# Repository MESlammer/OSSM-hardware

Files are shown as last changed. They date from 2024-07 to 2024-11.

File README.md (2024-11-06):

# OSSM - Open Source Sex Machine



OSSM (pronounced like "Awesome") is a user friendly every day sex machine for the people.

This project aims to help people curious about sex machines explore their interest. A second objective is optionally
learning how mechanics, electronics, physics and computing are involved in your sexual pleasure.

Please note that this is a _work in progress_ and we have attempted to keep compatibility with the current BOM going
forward, but it's not guaranteed.

_Our Primary design goals_ are to make a machine that is compact, quiet, of moderate cost, 3D printable (no
cutting/machining required), flexible, highly performant, with easily sourced components, and doesn't look like a giant
machine.
<p align="center">

</p>

### Is it actually Open Source?

It is one of a kind Certified, Actual, Factual, Open Source

[](https://certification.oshwa.org/ca000057.html)

## Getting Started

### [Read the Frequently Asked Questions](FAQ.md)

There are a few hardware flavours to choose from, we've included community modified versions in case that fits your use
case better!

### [Build Instructions](Documentation/Assembly%20Instructions.pdf)

### [Build Videos]("https://youtube.com/playlist?list=PLzSK7OAu3KNQsFo6WJGT8P28lfkD3xpps")

[Join our Discord](https://discord.gg/MmpT9xE) to be part of the discussion and get help with your build. We have a huge community of
makers!

<p align="center">

</p>

### Software

The software is available in this github repository. It is written and compiled utilizing PlatformIO on Visual Studio
Code. [Reference for working with the code in PlatformIO here](OSSM PlatformIO Readme.md)

We recommend using
the [Research and Desire Reference Board](https://shop.researchanddesire.com/products/ossm-reference-board) as Do It
Yourself by someone without extensive electronics knowledge creates a lot of support overhead. This code is still
arduino IDE compatible but offers many times better performance. Web based control is projected to be available in Feb 2025.  
### Eagle PCB

Simple PCB to power an ESP32 (wifi enabled microcontroller) from 24V and breakout the pins for the OSSM control

### Mechanical design

The OSSM use a compact belt design with components that have become widely available due to 3D printing popularity.
It is driven by a Nema23 motor of **your** choosing, although we reccomend small integrated closed loop servos for their
silent operation and very high performance.
<p align="center">

</p>

### Mounting

We have a new stand design you can check out on onshape!
[OnShape link](https://cad.onshape.com/documents/d520ea9a8cadb4ae8681f59b/w/00b211a6fa3b76c59ef28f4e/e/5f2c80d9d9c2433a7be7f789)

OSSM on mounting solution

### Safety

The safety of the OSSM build is yet to be fully characterized as it is a work in progress. The OSSM is a framework for
building your own sex machine and as such your specific combination may have risks not inherent to other builds. These
risks may be undocumented or undiscovered. Please see the [Hazards](Documentation/Hazards.md) file for more
information.

While using the OSSM we can suggest the following hierarchy of safety, however it is up to you and your build to decide
what risks exist and how to mitigate them.

1. Have ability to move away
2. Have ability to remove the power
3. If you are in bondage, safety is responsibility of the Top

## Bill Of Materials

We are calling this the reference build, when deviating from it please check compatability with existing Bill Of
Materials (BOM)

1.  **[3D Printed Parts](Hardware/OSSM%20Printed%20Parts)**
    - This has recently had significant changes
    - [Make sure to choose one of the options for the toy adapters](Hardware/OSSM%20Printed%20Parts/end%20effector%20options)
    - There are several mounting options available, the most popular being  
      the [Ulanzi Ball head mount](Hardware/OSSM%20Mounting) or  
      the [Shicks mount](Hardware/OSSM%20Mounting/Shicks%204040%20mount)
    - Thank you @Elims for the [belt tensioner design]( https://github.com/theelims )

2.  **IHSV57 NEMA23 Servo with 8mm shaft** _or_ **57AIM30 (Gold Motor)**:
    - **Gold Motor**
      - New standard motor for OSSM, please see [Gold Motor Info](Documentation/Gold-Motor.md) while docs are being updated.
        This motor is cheaper, more compact and has improved features which are being implemented in OSSM firmware.
      - For the latest information about this change, join the KinkyMakers Discord.
    - **iHSV57 (Previous Standard Motor)**
      - _Avoid the StepperOnline version_
      - Make sure you get something with **8mm** shaft.
      - There are **3** sizes of this motor:  
          100W = [iHSV57-30-**10**](https://www.aliexpress.com/w/wholesale-iHSV57%2525252d30%2525252d10.html)

          140W = [iHSV57-30-**14**](https://www.aliexpress.com/w/wholesale-iHSV57%2525252d30%2525252d14.html)

          180W = [iHSV57-30-**18**](https://www.aliexpress.com/w/wholesale-iHSV57%2525252d30%2525252d18.html)

      - We recommend motors with firmware version 6 (shown as `V60x`). Pay attention to
        this, [the firmware version is printed on the label on the side.](https://user-images.githubusercontent.com/131713378/234460307-1c29c18b-3bb5-4ac9-b66f-0dea9df0acac.png)
        You cannot update the motor firmware. version 5 will work, but it is not as feature rich for potential new
        features.
      - Search around for the best deal for you - we reccommend searching "ihsv57" on Aliexpress.com and choosing the -10
        -14 or -18. Some example listings:

        [AliExpress - US](https://www.aliexpress.us/item/2251832528412325.html)

        [AliExpress - CA & AU](https://www.aliexpress.us/item/32714727077.html)

      - For details on picking the right motor for your use case - check
          this [FAQ](FAQ.md#q--what-strength-of--motor-do-i-need)
      - If you are using the 140W or 180W version it is recommended to use a 10mm wide belt and pulley (see the next two items)

3.  **GT2 Pulley 8mm Bore 20 Tooth, 10mm width** :

    [Amazon - CA](https://www.amazon.ca/Timing-Pulley-8mm-bore-10mm-belt-20-Tooth/dp/B09L7D7HHT)

    [Amazon - US](https://www.amazon.com/WINSINN-Aluminum-Synchronous-Timing-Printer/dp/B07BTDRW5Z)

    [Banggood - AU](https://au.banggood.com/5MM-or-6_35MM-or-8MM-Bore-20TeethGT2-Alumium-Timing-Pulley-For-Width-10mm-GT2-Belt-p-1106314.html)

4.  **GT2 Timing Belt - 10mm width** :

    [Amazon - CA](www.amazon.ca/Timing-Meters-Creality-Anycubic-Printer/dp/B097T4DFM6)

    [Amazon - US](https://www.amazon.com/Timing-Meters-Creality-Anycubic-Printer/dp/B097T4DFM6)

    [Amazon - AU]()

    - Your desired stroke length plus about 200mm should be your minimum order length

5.  **Bearings** MR115-2RS 5x11x4mm :
    [Amazon - CA](https://www.amazon.ca/gp/product/B07CVBW44R)

    [Amazon - US](https://www.amazon.com/Miniature-Bearings-MR115-2RS-Double-Shielded-5x11x4mm/dp/B08PFT72RQ)

    [Aliexpress - AU](https://www.aliexpress.us/item/2251832628223170.html)

6.  **MGN12H Rail and bearing** :

    [Amazon - CA](https://www.amazon.ca/MGN12H-Stainless-Carriage-Precision-Machine/dp/B09TWKWCZR)

    [Amazon - US](https://www.amazon.com/ReliaBot-Linear-Carriage-Printer-Machine/dp/B07B4DWWZC)

    [Aliexpress - AU](https://www.aliexpress.com/item/32840113910.html)

    - Minimum 250mm in length, suggested 350mm
    - Rail length = desired stroke + 180mm
    - Must be MGN**12H** rail - H is a longer car than C which gives greater stability. 12 indicates 12mm rail width.

7.  **Power Supply**: 24 volt 4-5 amp w/ 2.1mm barrel DC plug

    - Larger motors generally need more power!  
      180W -> 24V 5A suggested minimum  
      140W -> 24V 4A suggested minimum  
      100W -> 24V 4A suggested minimum

    - See the FAQ for more details about power supply sizing based on real world experience of OSSM users.
    - The OSSM will work with small power supplies, but will be limited on maximum force.
    - Ensure the power supply is fully enclosed and shielded to avoid cross talk from electromagnetic interference (like a laptop power supply).
    - Ensure the power supply has the correct approvals for your location - This really helps ensure performance as well! (UL, CE, etc.)
    - It is strongly recommended that you purchase a good quality PSU such as a Meanwell.

8.  **Metric Hex Cap Screws** :  
    [Amazon - CA & US](https://www.amazon.ca/Comdox-500pcs-Socket-Screws-Assortment/dp/B06XQLTLHP)

    [Amazon - AU](https://www.amazon.com.au/VIGRUE-Stainless-Hexagon-Washers-Assortment/dp/B08CK9Y971) (this is a little
    expensive, we are looking for a cheaper alternative)

    - A kit like the ones above will provide what's needed:
    - 4x m5x20
    - 1x m5x12 (can also use m5x20)
    - 10x m3x8
    - 2x m3x16
    - 8x m5 nuts
    - 8x m3 nuts

9.  **ESP32 Development Board**
    - [An official OSSM reference PCB](https://research-and-desire.myshopify.com/collections/all/products/ossm-reference-board)
    - We do not currently have a best suggestion if you are not using a reference board, most generic development boards are the same
    - We have found that the 3.3v boards may miss steps at high speed, so please use a level shifter as well.
    - To start working on the project, something like this [Adafruit board](https://www.adafruit.com/product/3405) is an excellent place to start.
    - Accessories required for prototyping
      include [Breadboard](https://www.amazon.ca/Breadboard-Solderless-Prototype-Distribution-Connecting/dp/B01EV6LJ7G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)
      and [Dupont Jumpers](https://www.amazon.ca/120pcs-Multicolored-Breadboard-Arduino-raspberry/dp/B01LZF1ZSZ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)

### Octopart Links for ease of ordering and tracking

A list of non-3d printed supplies in one place. Most of the parts aren't available through the preferred Octopart
vendors but it still makes for a convenient list.

[Octopart - Collected Bill of Materials for US Suppliers](https://octopart.com/bom-tool/nfUsbySS)

## Official OSSM Wiring

OSSM reference board front
The above image is of a version 1 reference board.

### OSSM PCB Connections

OSSM PCB connection diagram

### GPIO Layout

OSSM pinout diagram
JST Header location with pin labels

## Non-Official OSSM Wiring

This should be a good start for the wiring of your OSSM! However, depending on your hardware mix settings or wiring may
be different

### OSSM PCB w/ TB6600 Stepper Driver



### Servo Wiring

ServoWiring

### Stepper Wiring

wiring notes

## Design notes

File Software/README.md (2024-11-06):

# Software
This is the recommended software for use with OSSM designs

## Requirements:
- Arduino IDE or PlatformIO
- ESP32 microcontroller

To use with Arduino, simply open the .ino file in the src directory. You will also need to copy the folders in the lib directory to your arduino library folder on your PC.

Use the tutorial below to install the ESP32 board into your Arduino IDE so you're ready to program!

[Setting up ESP32 on Arduino IDE](https://randomnerdtutorials.com/installing-the-esp32-board-in-arduino-ide-windows-instructions/)

If you aren't sure what ESP board to select in Arduino IDE, choose "ESP32 Dev Module" - it works on all ESP32 I have tested so far.

ESP32 Architecture

## Logging

This project uses ESP32's [native logging library](https://docs.espressif.com/projects/esp-idf/en/stable/esp32/api-reference/system/log.html).

## Commands

**Upload and monitor**
```bash
pio run -t upload -t monitor
```

**Run Unit Test tests**
```bash
pio test -e test
```

## Other Documentation
- [Git Branching Strategy](docs/Git Branching Strategy)

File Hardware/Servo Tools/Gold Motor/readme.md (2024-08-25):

<h1> New Web Serial tool </h1>

in the "Javascript GMP" folder run the page in some browser that supports web serial and hopefully it'll just work. 



<h1> Old Python Script </h1>
This pyhton script will write the default changes to the gold motor and show all the current settings in mostly english



the settings we change by default are



Watch out, I got tired of using the tool provided by the vendor and this was done quickly one night with ChatGPT as my copilot...

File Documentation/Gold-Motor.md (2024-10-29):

# New Standard Servo Motor

## 57AIM30 - Gold Motor

We have been testing and have decided on a new motor as the build standard. It has the same mounting pattern and shaft diameter as the old motor (iHSV57-30-XX).
It is sold by Research and Desire as [Gold Motor](https://www.researchanddesire.com/products/ossm-motor-gold-motor) or available generically as 57AIM30

If you wish to order a 57AIM30, you should source a model that runs at 1500 RPM and has an RS485 interface (NOT the 3000 RPM or CANBUS versions)

Also note that if you source your motor from somewhere other than R&D, you will need to reprogram the stored settings with a USB to RS485 dongle using the scripts found [here](https://github.com/KinkyMakers/OSSM-hardware/tree/master/Hardware/Servo%20Tools/Gold%20Motor) before you can use it.

Advantages:

- Cheaper (20%) - dependant on availability and location.
- Smaller (40% length of 180W standard - i.e. 60% reduction!).
- Lighter (50% weight of 180W).
- Higher peak force (30% higher in real-world test).
- Better over-torque handling - can be configured to reduce torque output instead of disable like current 180w servo.
- Is drop-in replacement for iHSV57 series making BOM compatible.

Requirements:
- Requires V2.2 PCB or newer for  simple wiring with PH-4 cable
  - Older boards will need wires soldered to 10 pin header
  - Recommend adding 1500uF capacitor, min 50V to older boards <V2.3

Disanvantages:

- More efficient (this causes more regenerated power in some motion conditions which requires additional capacitance and handling on the PCB).
  - PCB v2.3 as currently sold by R&D or listed on this repo has added capacitor. If you are upgrading your motor, you should add the capacitor as shown below.
- Digital comms over RS485 (Not worse than current RS232, just current boards don't have the needed adapter).
- Requires software setup to see full benefits (default FW settings disable motor in over-torque condition).
- If modding your software, technically lower top speed than HSV. (Standard code speed limit is lower than gold motor limit, so not a disadvantage for regular user).

## 42AIM30 - Gold Motor 42 (variant)

In addition to 57AIM30 (Gold Motor), which fits exactly to the previous designs and specs with no extra work, there is a varient motor which has exactly same internals and specs.
The 42AIM30 (see notes above for ordering the correct model) does away with the heatsink housing and is purely the cylindrical motor with connectors at the base.

Advantages (compared to 57AIM30):

- Smaller diameter (26%) - plus cylinder vs square.
- Lighter (unknown - ~25%?) - please submit mass if you have one.

Disadvantages (compared to 57AIM30):

- Much harder to mount.
  - No _mounting ears_ to bolt through, must put exact length machine screws into face of motor.
  - Current standard housings are not compatible with 42AIM30, though there are some options available via discord.
- Suspected heat issues caused by lack of heat sink and enclosure in printed housing - more data needed.
- Lack of clear advantages over Gold Motor (57AIM30)
  - Same specs.
  - Same length.
  - Same disadvantages.
  - Changes to BOM required.

OSSM Gold Motor Wiring





OSSM Capacitor view

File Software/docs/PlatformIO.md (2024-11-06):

OSSM has been developed in PlatformIO.  For people used to the Arduino IDE, moving to PlatformIO can seem daunting.  Trust us that it is simpler than it looks to operate and works far better than the very basic Arduino IDE as the project grows and changes.  

This is particularly important when it comes to managing all the libraries and dependencies. This gets very complex, very quickly. Earlier builds of OSSM it was sort of possible to mash it into the Arduino IDE and get a compile happening.  It has now past the point when it is easier to teach you to use PlatformIO than it is to repackage OSSM for the Arduino at each release. 

Why? More time for coding features and easier collaboration! OSSM is moving fast. Once you get used to VSCode there are some other great features such automatic downloads from Github and linting (autocomplete for code). 

1. Start by installing VSCode and the PlatformIO extension. There are plenty of guides for this on the web.  

2. Restart VSCode wait until PlatformIO has started and look on the sidebar for this button.



3. Click "Open"



4. This will pop up 



5. Click "Open Project" and search for the OSSM directory that has platformIO.ini in it





6. In the src directiory you should find main.cpp, click on that 



7. Near the bottom of the window look for a tick (compile) and an arrow (upload) 

 

8. You can then compile or skip that step and upload directly to your board.  

What if that doesn't work?  Check the debug screen but chances are you have not selected the right Com port for the OSSM board or the wrong board for the project.  

9. COM or /DEV/TTY will vary from machine to machine. It is set here in platformIO 



11. The reference board for OSSM has an embedded "Espressif ESP32 Dev Module".

12. If the project fails to build and the upload fails DON'T PANIC! Chances are there has been some kind of external library update.  Try changing the following lines in platformIO.ini in the root of the project 

"platform = espressif32"   to "platform = espressif32@3.5.0"

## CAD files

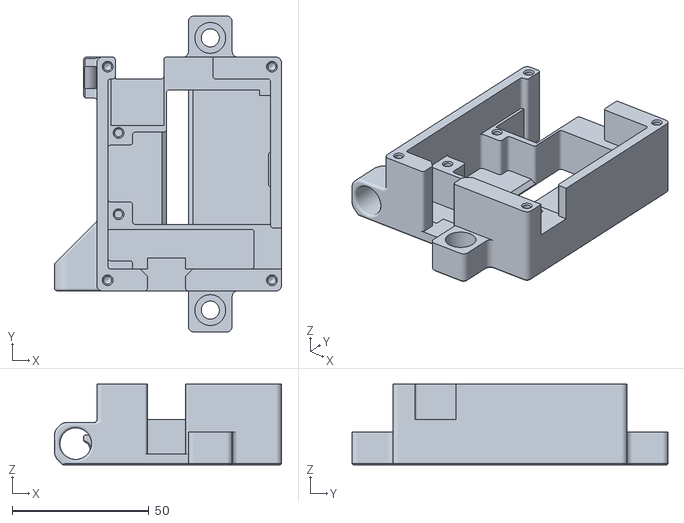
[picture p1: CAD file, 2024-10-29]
Hardware/OSSM Printed Parts/OSSM - PCB Mount - Box.stl
82.9 x 115.4 x 29.5

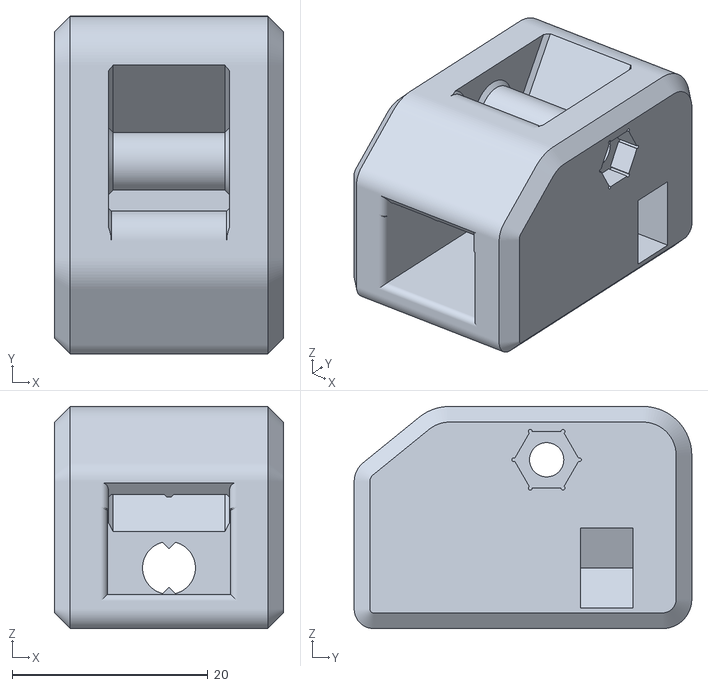
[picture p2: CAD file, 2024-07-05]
Hardware/OSSM Printed Parts/OSSM - Belt clamp - Tensioner end.stl
23.4 x 34.5 x 22.7

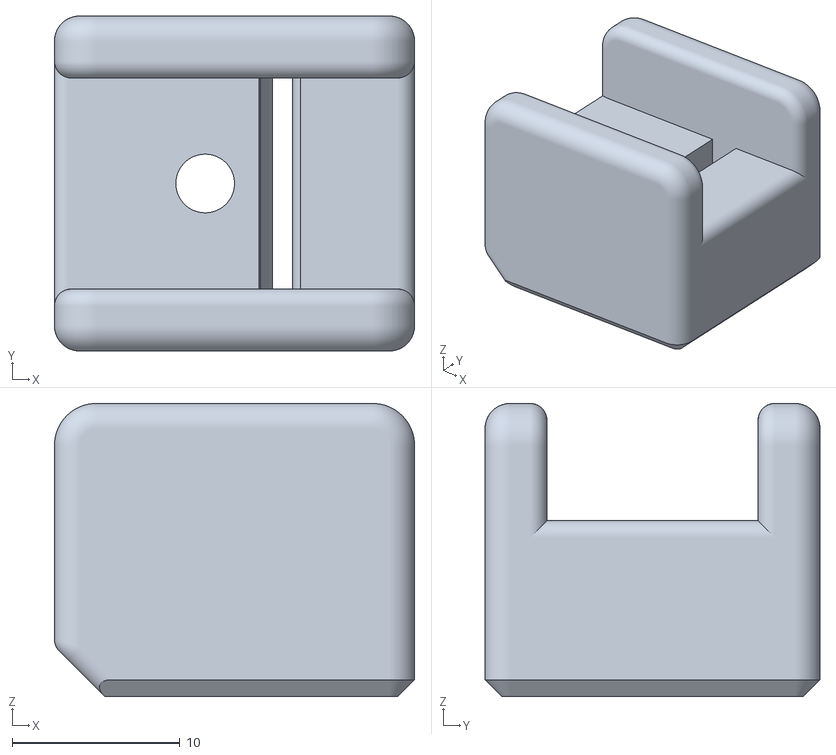
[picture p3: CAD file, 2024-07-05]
Hardware/OSSM Printed Parts/OSSM - Belt clamp - Top.stl
21.5 x 20.0 x 17.5

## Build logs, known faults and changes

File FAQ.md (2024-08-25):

# Frequently Asked Questions

### Q: What is OSSM?

A: An OSSM is compact sex machine that can be customised to suit you.  Based around a NEMA23 pattern for electric motors it can be driven by stepper or best of all servo motors it uses a combination of 3D printed and off the shelf parts.

### Q: Why go to all this trouble?  Why don't you just buy a ready made machine?

A: The OSSM is open you are not tied to a specific company and it does a lot more than equivalently priced machines.  Best of all you can fully control the stroke speed and most importantly depth.  You can make patterns or even your own control software.  Maybe you want to add a stroker rather than a dildo, you can modifiy it to do that.  Not enough power? You can use a bigger motor up to a certain point.

### Q: What parts do I need?

A: Head over to [the README](./#bill-of-materials) - the BOM is maintained there.
  
### Q: I've been reading about motors and now I'm really confused
  
A: While you can theoretically use any Nema23 mount motor.  There are motors that work and some that work better.  Stepper motors are cheaper and noiser so the community recommends closed loop servo motors.  These are more efficient and more importantly easier to program.  

### Q:  What strength of motor do I need?
  
A: That depends on a couple of factors.  

- Vaginal or Anal use
- Size of toys
- Anticipated Speed
  
We don't have a lot of recorded data [Please help us with this!] however the general suggestions are;

- **NEW 57AIM30 (Gold Motor)**: Roughly equivalent to **180W** below, see [Gold Motor Info](https://github.com/KinkyMakers/OSSM-hardware/blob/master/Documentation/Gold-Motor.md) and BOM.
- **100w** IHSV57 Servo: Vaginal usage with medium size toys and Anal usage with smaller toys (10 lbs force)
- **140W** IHSV57 Servo: Vaginal usage with larger toys, Anal use with medium size toys (15 lbs force)
- **180w** IHSV57 servo works with a wide range of toys for vaginal or anal play, and really packs a punch (20 lbs force). However if you like seriously heavy fantasy dildos you might want to consider building a Squooter [see the discord] that uses and even a larger motor mount; the NEMA34 which has even more powerful motors.

A build with a servo motor will have a flat torque curve across the speed range. That's to say - it will push just as hard at the slow speeds as well as the fast.
  With a stepper, the most force will be at the slower speeds and the top speed of a stepper is much less than the servo we've chosen to work with.
  
### Q: Hold on, why does anal play need more powerful motors?

A: Butts have big powerful muscles! It's common for people to bear down, or clench when things are feeling really good. Also it can be pretty fun shoving big objects in there! It can take a big motor to handle a big toy in a poweful butt.

### Q: What sized 3D printer do I need?

A: The minimum bed size is 105mm x 105mm for the largest single piece. Approximately 125mm of height is required for the shorter vac-u-lock compatible adapter, the plate is significantly shorter.

### Q: What print material is best?

A: All of our testing has been with simple PLA, however if you do print it in an interesting material make sure to share it to the discord!

### Q: What is the infill percentage?

A: 30% has been found to work just fine with PLA for non flexible parts

### Q: How thick are the walls and top?

A: Recommend at least 3mm for non flexible parts.

### Q: What are these flexible parts and how should I print them?

A: There are mounting solutions that use clamps for the OSSM these need some flexiblity.  For these parts thinner walls 2mm, lower infill percentages and a gyroid pattern.

### Q: How do I mount toys onto the OSSM?

A: Aside from the motor this is second decision.  There is a vacc-u-lock compatible mount the double double and a plate mount for suction cup toys that has some points to tie a dildo down The OSSM Platten

### Q: What to I mount the machine on?  

A: Well there are a few designs available.  THere are standard pipe mounts for US/Canadian along with 80/20 rails that can be used like a construction set.  There are even manfrotto boom compatible adaptors.  It is really limited by you imagination.

### Q: How do I control my OSSM

A: It depends on how you are going to use it.  Basic OSSM control is via the wired remote and a more advanced remote is available from community members (M5 Remote).  If you want something specific you can create your own that is the great thing about open source hardware.

### Q: I heard somewhere you can "control via a web page?"  Can I get people to control my OSSM over the internet?

A: As of August 2023 you cannot control an OSSM over the internet.  In the past R&D offered a web page that allowed very basic control with speed and depth settings over wifi.  

### Q: X-Toy and funscript support.  Where is it?  

A: As of August 2023 there is a highly experimental X-toy firmware forked from an earlier version that requires endstops.  This code has significant issue and is not considered to be safe for use on humans. There are frequent pauses, it loses track of where it is and has a tendency to randomly extend to maximum depth. Development of an X-Toys firmware is happening but it is complicated.

### Q: Why is X-Toys/Funscripts/ButtplugIO so difficult?

A: Things are a lot more complicated once you dig down into them.

- The motion core does not yet support position streaming. This is in development and requires a complete redesign of the safety architecture as you don't want to accidentally stab yourself.
- From the experimental software we learnt that the latency margin is really thin, Bluetooth especially struggles here. This will be a challenge to overcome.
- The data models of both xtoys and Buttplug.io do not support complex data models as it would be required for OSSM out of the box. As scaling to the full length of OSSM is just not an option. There might be a workaround by emulating an other toy. But you won't be able to control all aspects of OSSM through this.

### Q: There is an OSSM reference board do I have to buy it to make an OSSM?

A: No you don't but it does make building an OSSM a lot easier and stops you having to solder anything.  

### Q: Powersupplies what size do I need?

A: That is linked to the size of motor.  The higher the wattage of motor the larger the powersupply you need.  For safety use a desktop power supply that is ideally double insulated. Power supplies from Mouser/Digikey/Conrad/RS etc are all typically more expensive than "no brand supplies" you get from AliExpress/eBay/Amazon. Experience has been mixed with unbranded supplies with occasional quality and longer term stability issues.  

- 100w JMC we currently suggest a 4A 24V Supply
- 140w /180w JMC we currently suggest a 6A 24V

### Q: How long should the H-rail be?

A: It is really up to you but a 350mm rail will give approximately 195mm of depth.  

### Q: What is the size of the 24mm Thread for the End Effector?

A: It is a M24x3 (this is the size on the machine, do a test print for your new End Effector, you may have to upsize by 3-5%)

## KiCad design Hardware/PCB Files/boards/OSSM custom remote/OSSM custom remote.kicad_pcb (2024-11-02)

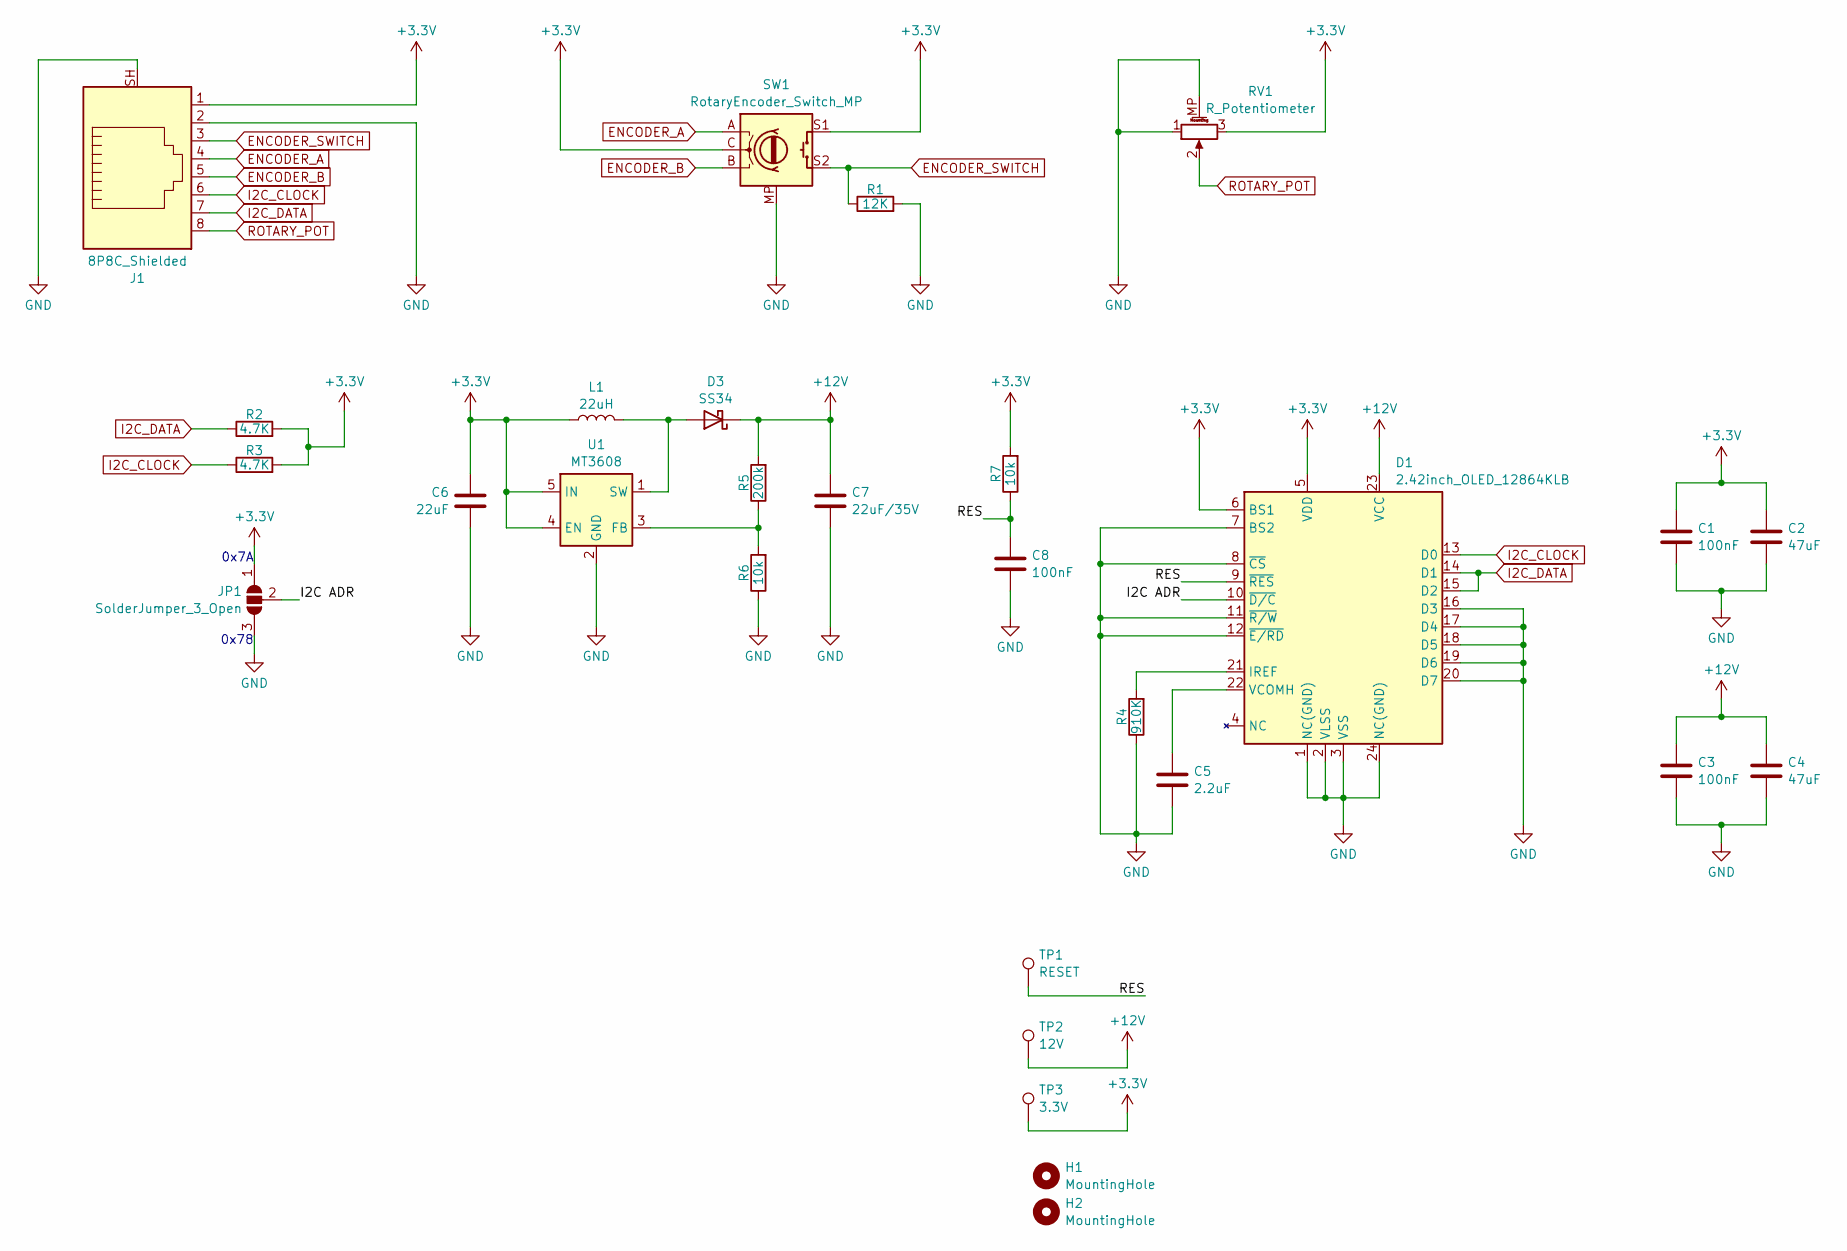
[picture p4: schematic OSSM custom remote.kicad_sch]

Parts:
C1, C3, C8: 100nF; C_0805_2012Metric
C2, C4: 47uF; C_0805_2012Metric
C5: 2.2uF; C_0805_2012Metric
C6: 22uF; C_0805_2012Metric
C7: 22uF/35V; C_0805_2012Metric
D1: 2.42inch_OLED_12864KLB; 2.42_OLED_24P_FPC_0.5MM
D3: SS34; D_SMA
H1, H2: MountingHole; MountingHole_3.2mm_M3_DIN965_Pad
J1: 8P8C_Shielded; RJ45_Molex_438605025_Horizontal; MPN 43860-5025
JP1: SolderJumper_3_Open; SolderJumper-3_P1.3mm_Open_RoundedPad1.0x1.5mm_NumberLabels
L1: 22uH; L_1812_4532Metric; MPN LQH43MN220K
R1: 12K; R_0805_2012Metric
R2, R3: 4.7K; R_0805_2012Metric
R4: 910K; R_0805_2012Metric
R5: 200k; R_0805_2012Metric
R6, R7: 10k; R_0805_2012Metric
RV1: R_Potentiometer; Potentiometer_Alps_RK09L_Single_Vertical; MPN RK09L1140A2U
SW1: RotaryEncoder_Switch_MP; RotaryEncoder_Alps_EC11E-Switch_Vertical_H20mm; MPN EC11E15244G1
TP1: RESET; TestPoint_Pad_D1.5mm
TP2: 12V; TestPoint_Pad_D1.5mm
TP3: 3.3V; TestPoint_Pad_D1.5mm
U1: MT3608; SOT-23-6; MPN MT3608

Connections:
+3.3V: C1.1, C2.1, C6.1, D1.5 (VDD), D1.6 (BS1), J1.1, JP1.1 (A), L1.1, R2.2, R3.2, R7.2, RV1.3, SW1.C, SW1.S1, TP3.1, U1.4 (EN), U1.5 (IN)
+12V: C3.1, C4.1, C7.1, D1.23 (VCC), D3.1 (K), R5.2, TP2.1
/I2C ADR: D1.10 (~D/C), JP1.2 (C)
/RES: C8.1, D1.9 (~RES), R7.1, TP1.1
ENCODER_A: J1.4, SW1.A
ENCODER_B: J1.5, SW1.B
ENCODER_SWITCH: J1.3, R1.1, SW1.S2
GND: C1.2, C2.2, C3.2, C4.2, C5.2, C6.2, C7.2, C8.2, D1.1 (NC(GND)), D1.2 (VLSS), D1.3 (VSS), D1.7 (BS2), D1.8 (~CS), D1.11 (~R/W), D1.12 (~E/RD), D1.16 (D3), D1.17 (D4), D1.18 (D5), D1.19 (D6), D1.20 (D7), D1.24 (NC(GND)), J1.2, J1.SH, JP1.3 (B), R1.2, R4.1, R6.1, RV1.1, RV1.MP (MountPin), SW1.MP, U1.2 (GND)
I2C_CLOCK: D1.13 (D0), J1.6, R3.1
I2C_DATA: D1.14 (D1), D1.15 (D2), J1.7, R2.1
unnamed: D1.21 (IREF), R4.2
unnamed: C5.1, D1.22 (VCOMH)
unnamed: D3.2 (A), L1.2, U1.1 (SW)
unnamed: R5.1, R6.2, U1.3 (FB)
ROTARY_POT: J1.8, RV1.2

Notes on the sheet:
0x7A
0x78

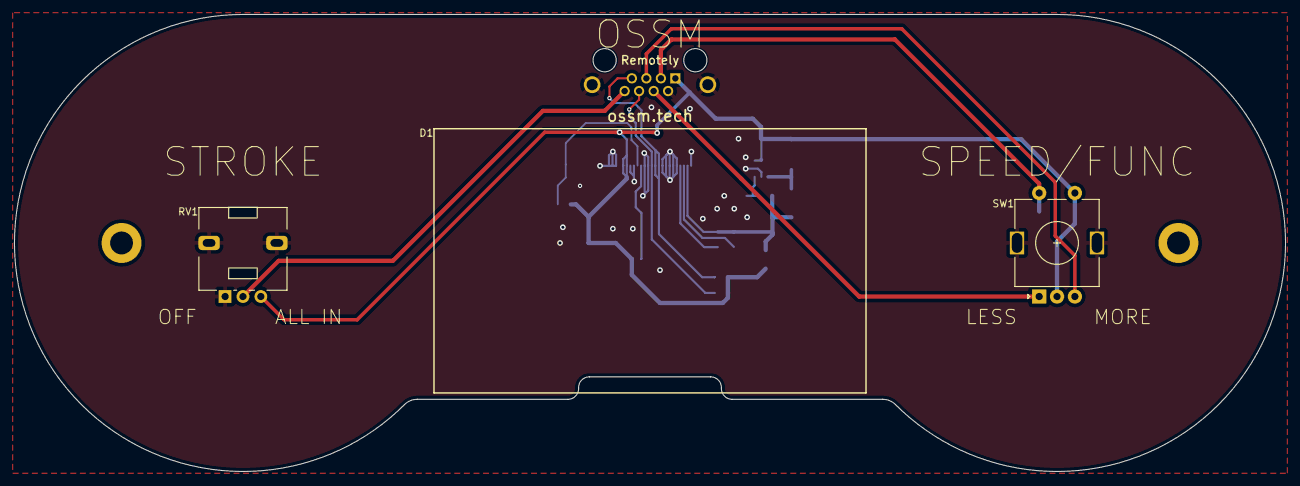
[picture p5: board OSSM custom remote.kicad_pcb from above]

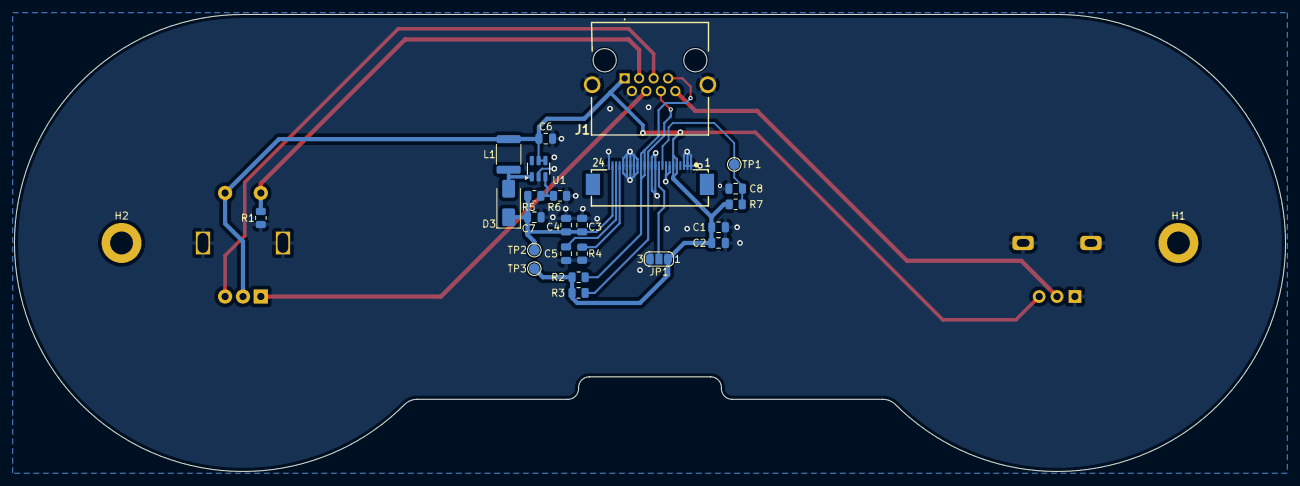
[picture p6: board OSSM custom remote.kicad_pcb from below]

Board: 2 copper layers, 178.0 x 64.0 mm, 28 parts (25 on the bottom side), 15 nets.

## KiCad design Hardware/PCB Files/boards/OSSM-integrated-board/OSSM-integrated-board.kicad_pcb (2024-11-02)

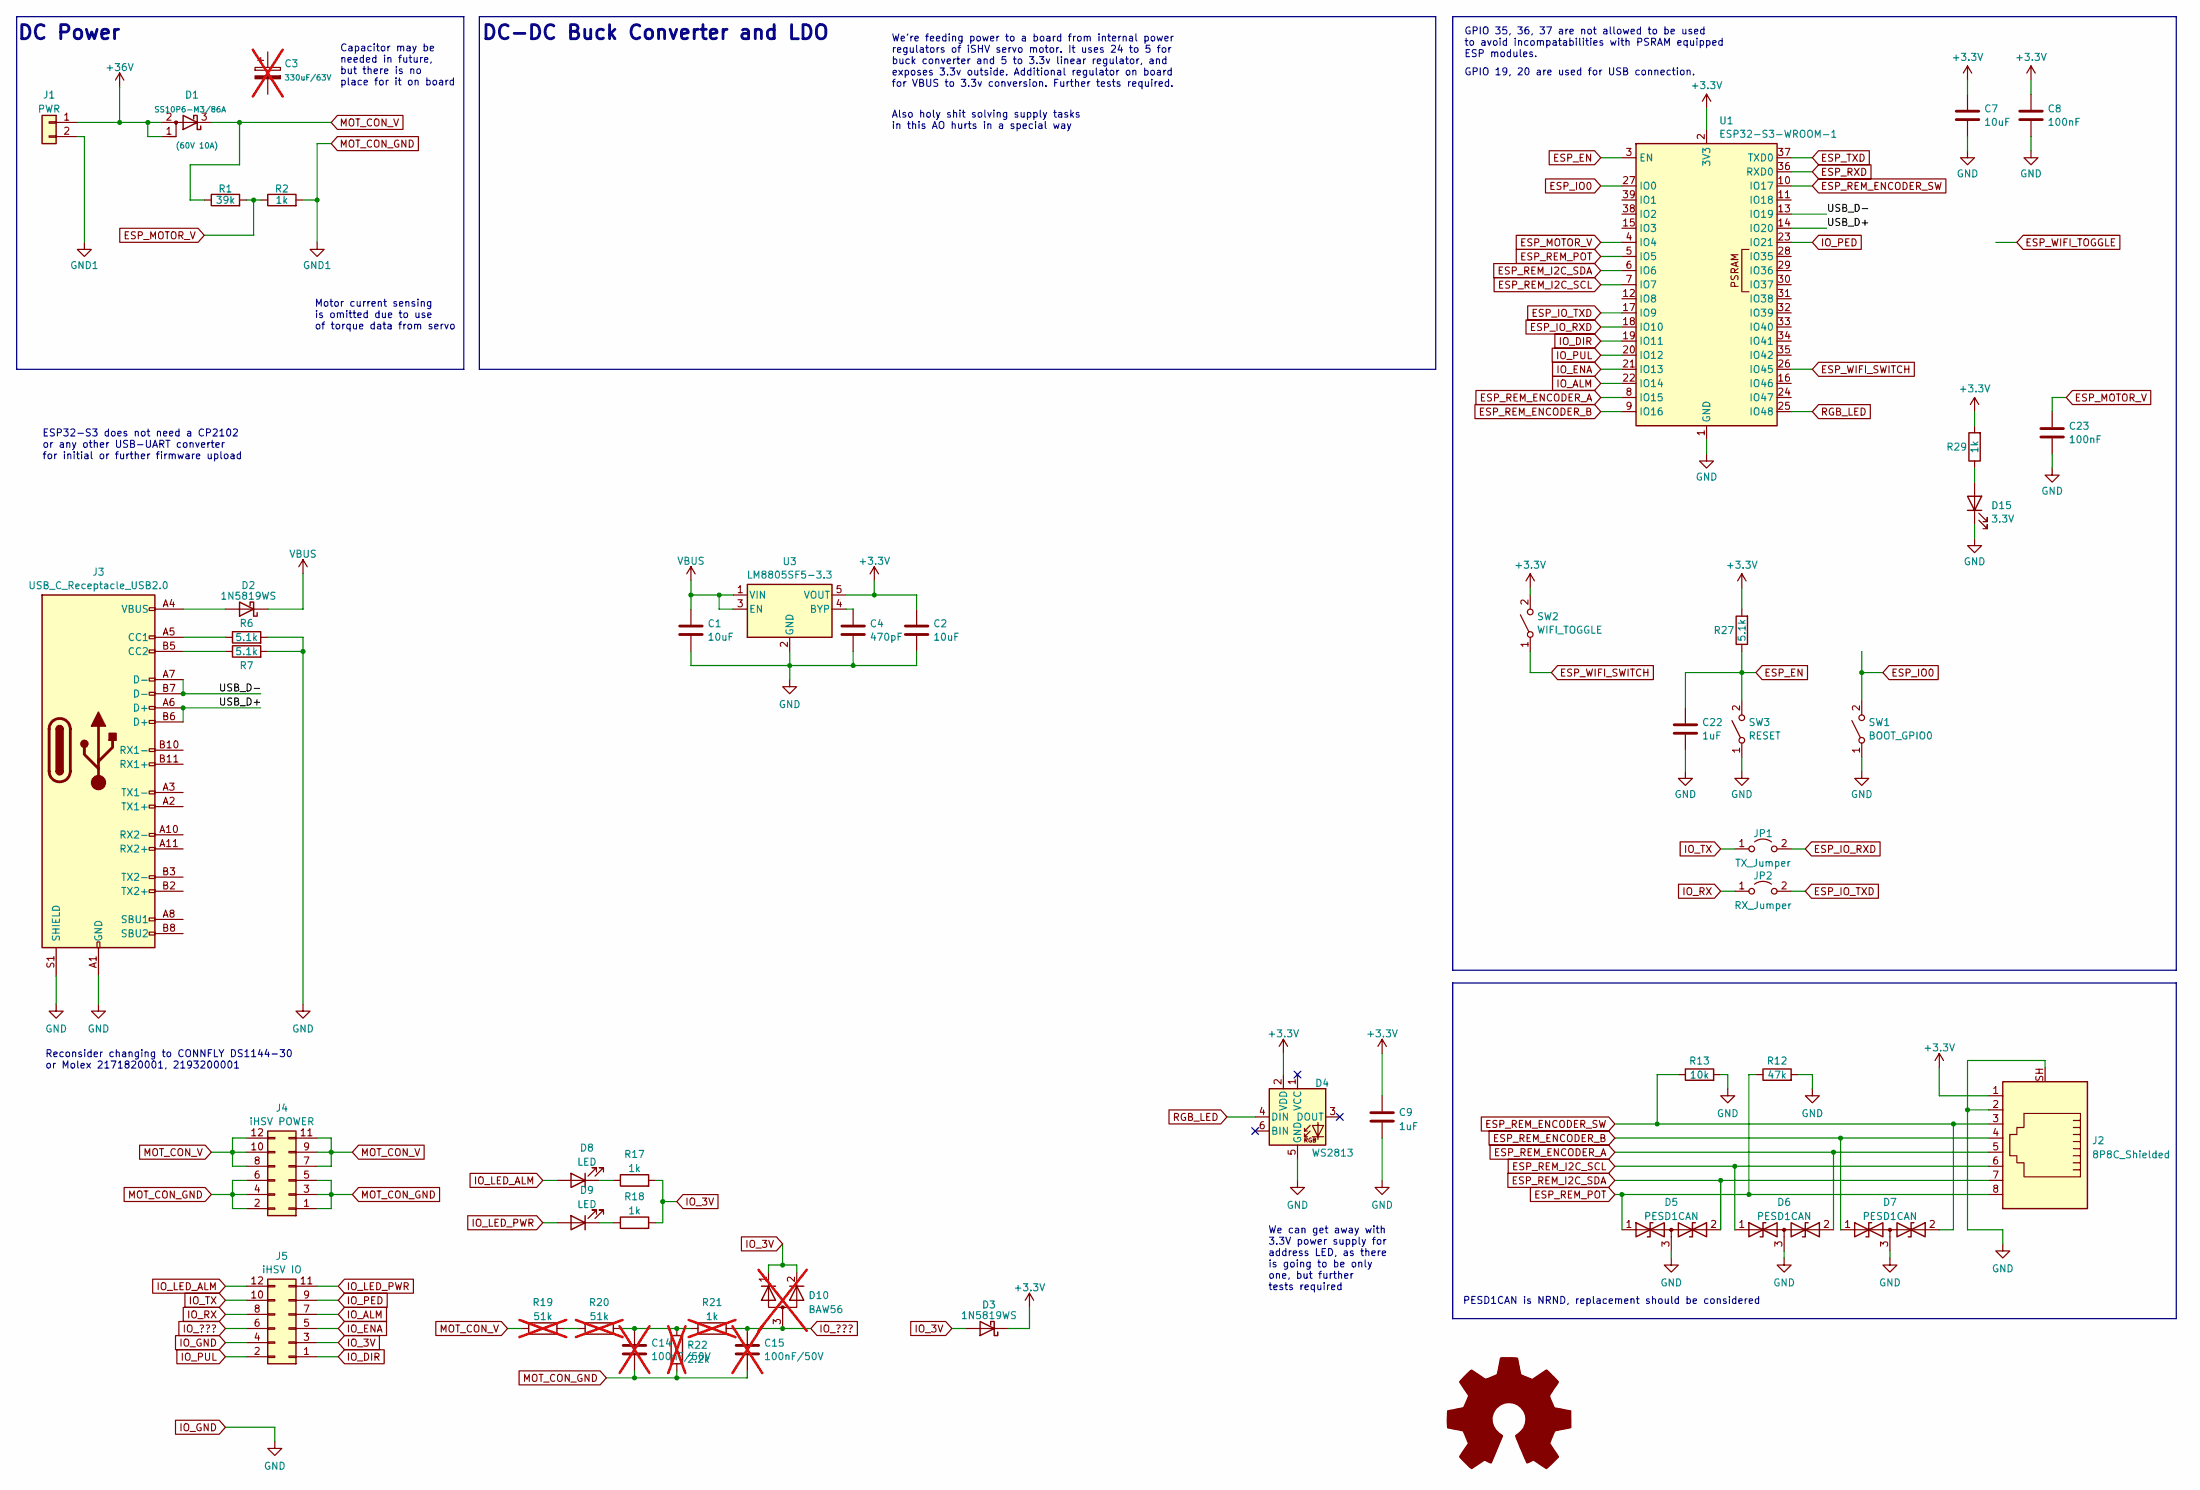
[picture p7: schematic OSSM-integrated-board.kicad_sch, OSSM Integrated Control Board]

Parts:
C1, C2, C7: 10uF; C_0402_1005Metric
C3: 330uF/63V; not fitted
C4: 470pF; C_0402_1005Metric
C8, C23: 100nF; C_0402_1005Metric
C9, C22: 1uF; C_0402_1005Metric
C14, C15: 100nF/50V; C_0805_2012Metric; not fitted
D1: SS10P6-M3/86A; TO-277A
D2, D3: 1N5819WS; D_SOD-323
D4: WS2813; LED_WS2812_PLCC6_5.0x5.0mm_P1.6mm
D5, D6, D7: PESD1CAN; SOT-23
D8, D9: LED; LED_0805_2012Metric
D10: BAW56; SOT-23-3; not fitted
D15: 3.3V; LED_0805_2012Metric
J1: PWR; Molex_Micro-Fit_3.0_43045-0212_2x01_P3.00mm_Vertical
J2: 8P8C_Shielded; RJ45_TE_1-338088-3_Vertical_Top_Entry
J3: USB_C_Receptacle_USB2.0; USB_C_Receptacle_Molex_204711-0001
J4: iHSV POWER; PinHeader_2x06_P2.00mm_Horizontal
J5: iHSV IO; PinHeader_2x06_P2.00mm_Horizontal
JP1: TX_Jumper; SolderJumper-2_P1.3mm_Open_TrianglePad1.0x1.5mm
JP2: RX_Jumper; SolderJumper-2_P1.3mm_Open_TrianglePad1.0x1.5mm
R1: 39k; R_0805_2012Metric
R2: 1k; R_0805_2012Metric
R6, R7, R27: 5.1k; R_0402_1005Metric
R12: 47k; R_0402_1005Metric
R13: 10k; R_0402_1005Metric
R17, R18, R29: 1k; R_0402_1005Metric
R19, R20: 51k; R_0402_1005Metric; not fitted
R21: 1k; R_0402_1005Metric; not fitted
R22: 2.2k; R_0402_1005Metric; not fitted
SW1: BOOT_GPIO0; SW_SPST_HRO_K2-1107ST
SW2: WIFI_TOGGLE; SW_SPST_HRO_K2-1107ST
SW3: RESET; SW_SPST_HRO_K2-1107ST
U1: ESP32-S3-WROOM-1
U3: LM8805SF5-3.3; SOT-23-5

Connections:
+3.3V: C2.1, C7.1, C8.1, C9.2, D3.1 (K), D4.2 (VDD), J2.1, R27.2, R29.2, SW2.2 (B), U1.2 (3V3), U3.5 (VOUT)
+36V: D1.1 (A), D1.2 (A), J1.1
/USB_D+: J3.A6 (D+), J3.B6 (D+), U1.14 (IO20)
/USB_D-: J3.A7 (D-), J3.B7 (D-), U1.13 (IO19)
ESP_EN: C22.1, R27.1, SW3.2 (B), U1.3 (EN)
ESP_IO0: SW1.2 (B), U1.27 (IO0)
ESP_IO_RXD: JP1.2 (B), U1.18 (IO10)
ESP_IO_TXD: JP2.2 (B), U1.17 (IO9)
ESP_MOTOR_V: C23.1, R1.2, R2.1, U1.4 (IO4)
ESP_REM_ENCODER_A: D6.2 (A2), J2.5, U1.8 (IO15)
ESP_REM_ENCODER_B: D7.1 (A1), J2.4, U1.9 (IO16)
ESP_REM_ENCODER_SW: D7.2 (A2), J2.3, R13.1, U1.10 (IO17)
ESP_REM_I2C_SCL: D6.1 (A1), J2.6, U1.7 (IO7)
ESP_REM_I2C_SDA: D5.2 (A2), J2.7, U1.6 (IO6)
ESP_REM_POT: D5.1 (A1), J2.8, R12.1, U1.5 (IO5)
ESP_RXD: U1.36 (RXD0)
ESP_TXD: U1.37 (TXD0)
ESP_WIFI_SWITCH: SW2.1 (A), U1.26 (IO45)
IO_3V: D3.2 (A), D10.1 (K), D10.2 (K), J5.3, R17.2, R18.2
IO_???: C15.2, D10.3 (A), J5.6, R21.2
IO_ALM: J5.7, U1.22 (IO14)
IO_DIR: J5.1, U1.19 (IO11)
IO_ENA: J5.5, U1.21 (IO13)
IO_GND: C1.2, C2.2, C4.2, C7.2, C8.2, C9.1, C22.2, C23.2, D4.5 (GND), D5.3 (common), D6.3 (common), D7.3 (common), D15.1 (K), J2.2, J2.SH, J3.A1 (GND), J3.A12 (GND), J3.B1 (GND), J3.B12 (GND), J3.S1 (SHIELD), J5.4, R6.2, R7.2, R12.2, R13.2, SW1.1 (A), SW3.1 (A), U1.1 (GND), U1.40 (GND), U1.41 (GND), U3.2 (GND)
IO_LED_ALM: D8.2 (A), J5.12
IO_LED_PWR: D9.2 (A), J5.11
IO_PED: J5.9, U1.23 (IO21)
IO_PUL: J5.2, U1.20 (IO12)
IO_RX: J5.8, JP2.1 (A)
IO_TX: J5.10, JP1.1 (A)
MOT_CON_GND: C14.2, C15.1, J1.2, J4.1, J4.2, J4.3, J4.4, J4.5, J4.6, R2.2, R22.2
MOT_CON_V: D1.3 (K), J4.7, J4.8, J4.9, J4.10, J4.11, J4.12, R1.1, R19.1
unnamed: C14.1, R20.2, R21.1, R22.1
unnamed: D2.2 (A), J3.A4 (VBUS), J3.A9 (VBUS), J3.B4 (VBUS), J3.B9 (VBUS)
unnamed: D8.1 (K), R17.1
unnamed: D9.1 (K), R18.1
unnamed: D15.2 (A), R29.1
unnamed: J3.A5 (CC1), R6.1
unnamed: J3.B5 (CC2), R7.1
unnamed: R19.2, R20.1
unnamed: C4.1, U3.4 (BYP)
RGB_LED: D4.4 (DIN), U1.25 (IO48)
VBUS: C1.1, D2.1 (K), U3.1 (VIN), U3.3 (EN)

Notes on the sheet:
GPIO 19, 20 are used for USB connection.
We're feeding power to a board from internal power regulators of iSHV servo motor. It uses 24 to 5 for buck converter and 5 to 3.3v linear regulator, and exposes 3.3v outside. Additional regulator on board for VBUS to 3.3v conversion. Further tests required.
Motor current sensing is omitted due to use of torque data from servo
We can get away with 3.3V power supply for address LED, as there is going to be only one, but further tests required
Capacitor may be needed in future, but there is no place for it on board
PESD1CAN is NRND, replacement should be considered
Reconsider changing to CONNFLY DS1144-30 or Molex 2171820001, 2193200001
DC-DC Buck Converter and LDO
GPIO 35, 36, 37 are not allowed to be used to avoid incompatabilities with PSRAM equipped ESP modules.
DC Power
ESP32-S3 does not need a CP2102 or any other USB-UART converter for initial or further firmware upload
Also holy shit solving supply tasks in this AO hurts in a special way

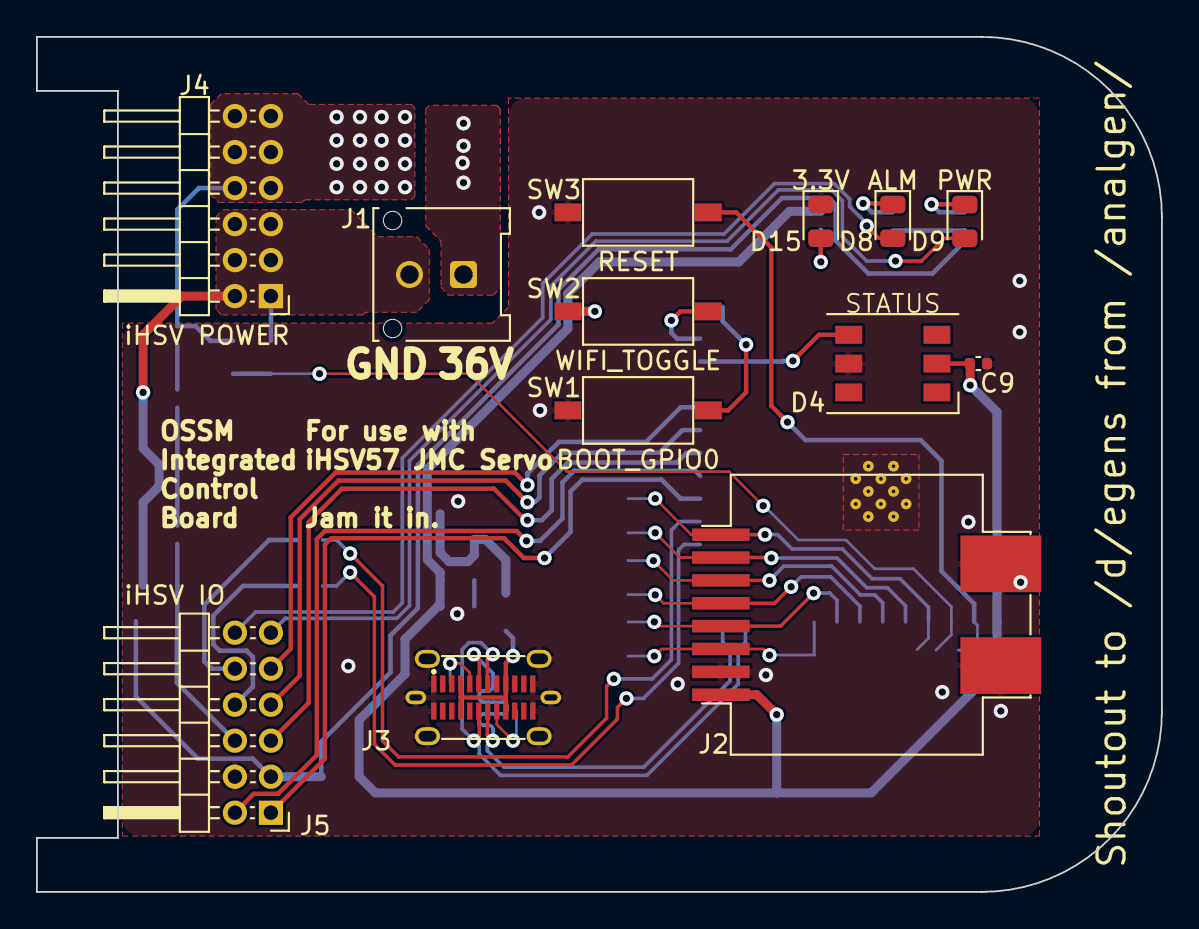
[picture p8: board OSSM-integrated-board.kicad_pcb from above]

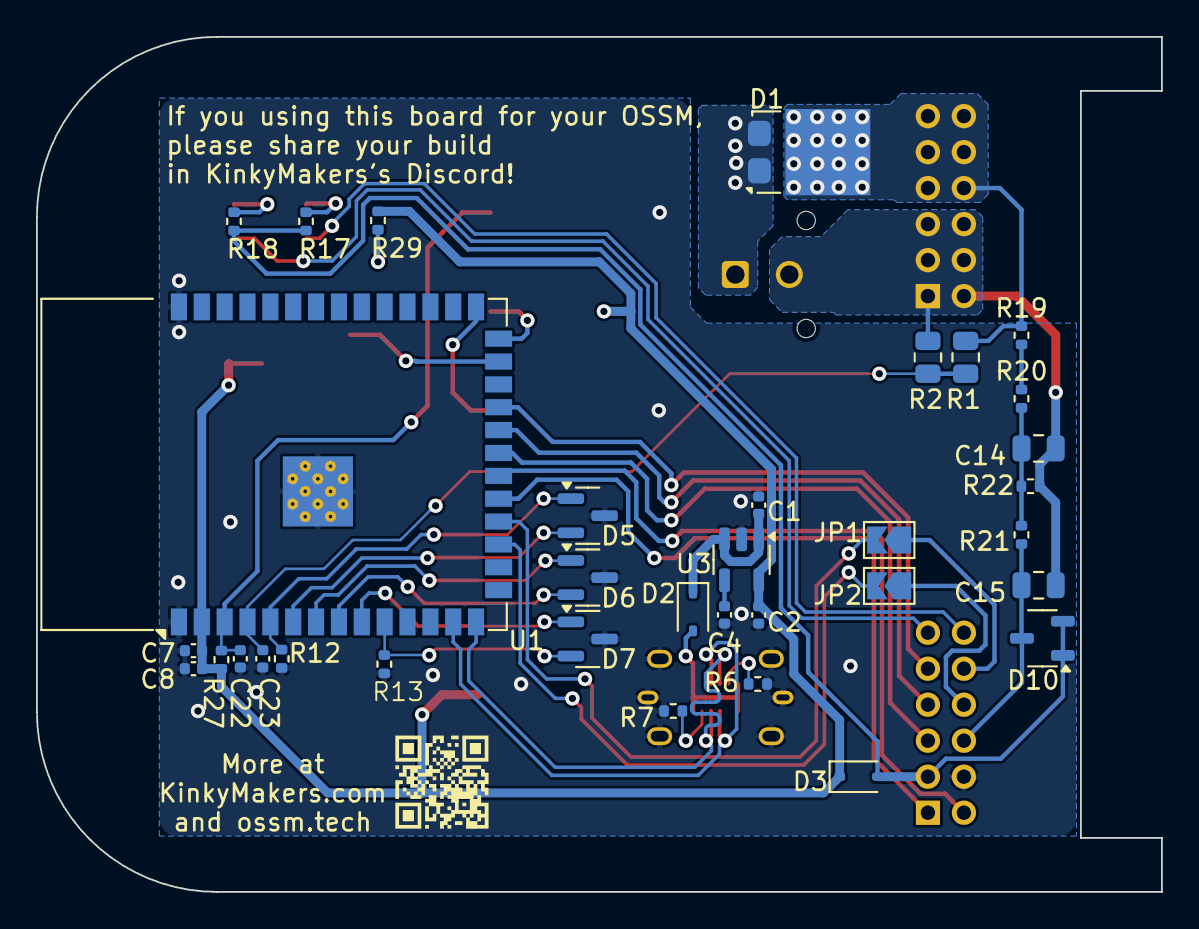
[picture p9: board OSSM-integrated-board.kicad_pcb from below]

Board: 2 copper layers, 62.5 x 47.5 mm, 47 parts (34 on the bottom side), 41 nets.

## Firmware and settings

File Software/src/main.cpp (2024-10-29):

#include "Arduino.h"
#include "OneButton.h"
#include "WiFi.h"
#include "ossm/Events.h"
#include "ossm/OSSM.h"
#include "services/board.h"
#include "services/display.h"
#include "services/encoder.h"
#include "services/stepper.h"
#include "services/modbus.h"

#include <FastLED.h>

#include "ModbusClientRTU.h"

#include "Logging.h"

/*
 *  ██████╗ ███████╗███████╗███╗   ███╗
 * ██╔═══██╗██╔════╝██╔════╝████╗ ████║
 * ██║   ██║███████╗███████╗██╔████╔██║
 * ██║   ██║╚════██║╚════██║██║╚██╔╝██║
 * ╚██████╔╝███████║███████║██║ ╚═╝ ██║
 *  ╚═════╝ ╚══════╝╚══════╝╚═╝     ╚═╝
 *
 * Welcome to the open source sex machine!
 * This is a product of Kinky Makers and is licensed under the MIT license.
 *
 * Research and Desire is a financial sponsor of this project.
 *
 * But our biggest sponsor is you! If you want to support this project, please
 * contribute, fork, branch and share!
 */

OSSM* ossm;

OneButton button(Pins::Remote::encoderSwitch, false);

CRGB leds [1];

void setup() {
    /** Board setup */
    initBoard();

    /** Service setup */
    // Encoder
    initEncoder();

    initModbus();
    // Display
    display.setI2CAddress(0x3C*2);
    display.setBusClock(400000);
    display.begin();

    FastLED.addLeds<NEOPIXEL, Pins::Display::ledPin>(leds, 1);

    leds[0] = CRGB::Red;
    FastLED.show();
    delay(500);
    leds[0] = CRGB::Green;
    FastLED.show();
    delay(500);
    leds[0] = CRGB::Blue;
    FastLED.show();
    delay(500);
    // Now turn the LED off, then pause
    leds[0] = CRGB::Black;
    FastLED.show();
    delay(500);

    ossm = new OSSM(display, encoder, stepper);
    // link functions to be called on events.
    button.attachClick([]() { ossm->sm->process_event(ButtonPress{}); });
    button.attachDoubleClick([]() { ossm->sm->process_event(DoublePress{}); });
    button.attachLongPressStart([]() { ossm->sm->process_event(LongPress{}); });


};

void loop() {
    button.tick();
    ossm->wm.process();
    //requestModbus();
};

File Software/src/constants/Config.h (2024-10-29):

#ifndef OSSM_SOFTWARE_CONFIG_H
#define OSSM_SOFTWARE_CONFIG_H

/**
    Default Config for OSSM - Reference board users should tweak UserConfig to
   match their personal build.

    //TODO: restore user overrides with a clever null coalescing operator
*/
namespace Config {

    /**
            Motion System Config
    */
    namespace Driver {

        // Top linear speed of the device.
        constexpr float maxSpeedMmPerSecond = 900.0f;

        // This should match the step/rev of your stepper or servo.
        // N.b. the iHSV57 has a table on the side for setting the DIP switches
        // to your preference.
        constexpr float motorStepPerRevolution = 800.0f;

        // Number of teeth the pulley that is attached to the servo/stepper
        // shaft has.
        constexpr float pulleyToothCount = 20.0f;

        // Set to your belt pitch (Distance between two teeth on the belt) (E.g.
        // GT2 belt has 2mm tooth pitch)
        constexpr float beltPitchMm = 2.0f;

        // This is the measured current that use to infer when the device has
        // reached the end of its stroke. during "Homing".
        constexpr float sensorlessCurrentLimit = 1.5f;

        // This is the measured torque that use to infer when the device has
        // reached the end of its stroke. during "Homing".
        constexpr int sensorlessTorqueLimit = 85;

        constexpr float stepsPerMM =
            motorStepPerRevolution / (pulleyToothCount * beltPitchMm);

        namespace Operator {
            // Define user-defined literal for unsigned integer values
            constexpr long long operator"" _mm(unsigned long long x) {
                return x * stepsPerMM;
            }

            // Define user-defined literal for floating-point values
            constexpr long double operator"" _mm(long double x) {
                return x * stepsPerMM;
            }
        }

        using namespace Operator;


        // This is in millimeters, and is what's used to define how much of
        // your rail is usable.
        // The absolute max your OSSM would have is the distance between the
        // belt attachments subtract the linear block holder length (75mm on
        // OSSM) Recommended to also subtract e.g. 20mm to keep the backstop
        // well away from the device.
        constexpr float maxStrokeSteps = 300.0_mm;

        // If the stroke length is less than this value, then the stroke is
        // likely the result of a poor homing.
        constexpr float minStrokeLengthMm = 50.0_mm;
    }

    /**
        Web Config
*/
    namespace Web {
        // This should be unique to your device. You will use this on the
        // web portal to interact with your OSSM.
        // there is NO security other than knowing this name, make this unique
        // to avoid collisions with other users
        constexpr char *ossmId = nullptr;
    }

    /**
        Font Config. These must be the "f" variants of the font to support other
       languages.
*/
    namespace Font {
        static auto bold = u8g2_font_helvB08_tf;
        static auto base = u8g2_font_helvR08_tf;
        static auto small = u8g2_font_6x10_tf;
    }

    /**
        Advanced Config
*/
    namespace Advanced {

        // After homingStart this is the physical buffer distance from the
        // effective zero to the home switch This is to stop the home switch
        // being smacked constantly
        constexpr float strokeZeroOffsetMm = 6.0f;
        // The minimum value of the pot in percent
        // prevents noisy pots registering commands when turned down to zero by
        // user
        constexpr float commandDeadZonePercentage = 1.0f;
        // affects acceleration in stepper trajectory (Aggressiveness of motion)

        constexpr float accelerationScaling = 100.0f;

    }

}

// Alias for "_mm" operator
using namespace Config::Driver::Operator;

#endif  // OSSM_SOFTWARE_CONFIG_H

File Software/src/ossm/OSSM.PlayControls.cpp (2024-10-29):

#include "OSSM.h"

#include "extensions/u8g2Extensions.h"
#include "services/tasks.h"
#include "utils/analog.h"
#include "utils/format.h"

void OSSM::drawPlayControlsTask(void *pvParameters) {
    // parse ossm from the parameters
    OSSM *ossm = (OSSM *)pvParameters;
    ossm->encoder.setAcceleration(10);
    ossm->encoder.setBoundaries(0, 100, false);
    // Clean up!
    switch (ossm->playControl) {
        case PlayControls::STROKE:
            ossm->encoder.setEncoderValue(ossm->setting.stroke);
            break;
        case PlayControls::SENSATION:
            ossm->encoder.setEncoderValue(ossm->setting.sensation);
            break;
        case PlayControls::DEPTH:
            ossm->encoder.setEncoderValue(ossm->setting.depth);
            break;
    }

    auto menuString = menuStrings[ossm->menuOption];

    SettingPercents next = {0, 0, 0, 0};
    unsigned long displayLastUpdated = 0;

    /**
     * /////////////////////////////////////////////
     * /////////// Play Controls Display ///////////
     * /////////////////////////////////////////////
     *
     * This is a safety feature to prevent the user from accidentally beginning
     * a session at max speed. After the user decreases the speed to 0.5% or
     * less, the state machine will be allowed to continue.
     */
    auto isInCorrectState = [](OSSM *ossm) {
        // Add any states that you want to support here.
        return ossm->sm->is("simplePenetration"_s) ||
               ossm->sm->is("simplePenetration.idle"_s) ||
               ossm->sm->is("strokeEngine"_s) ||
               ossm->sm->is("strokeEngine.idle"_s);
    };

    // Line heights
    short lh3 = 56;
    short lh4 = 64;
    static float encoder = 0;

    bool isStrokeEngine =
        ossm->sm->is("strokeEngine"_s) || ossm->sm->is("strokeEngine.idle"_s);

    bool shouldUpdateDisplay = false;

    // This small break gives the encoder a minute to settle.
    vTaskDelay(100);

    while (isInCorrectState(ossm)) {
        // Always assume the display should not update.
        shouldUpdateDisplay = false;

        next.speedKnob =
            getAnalogAveragePercent(SampleOnPin{Pins::Remote::speedPotPin, 50});
        ossm->setting.speedKnob = next.speedKnob;
        encoder = ossm->encoder.readEncoder();

        next.speed = next.speedKnob;

        if (next.speed != ossm->setting.speed) {
            shouldUpdateDisplay = true;
            ossm->setting.speed = next.speed;
        }

        switch (ossm->playControl) {
            case PlayControls::STROKE:
                next.stroke = encoder;
                shouldUpdateDisplay = shouldUpdateDisplay ||
                                      next.stroke - ossm->setting.stroke >= 1;
                ossm->setting.stroke = next.stroke;
                break;
            case PlayControls::SENSATION:
                next.sensation = encoder;
                shouldUpdateDisplay =
                    shouldUpdateDisplay ||
                    next.sensation - ossm->setting.sensation >= 1;
                ossm->setting.sensation = next.sensation;
                break;
            case PlayControls::DEPTH:
                next.depth = encoder;
                shouldUpdateDisplay = shouldUpdateDisplay ||
                                      next.depth - ossm->setting.depth >= 1;
                ossm->setting.depth = next.depth;
                break;
        }

        shouldUpdateDisplay =
            shouldUpdateDisplay || millis() - displayLastUpdated > 1000;

        if (!shouldUpdateDisplay) {
            vTaskDelay(100);
            continue;
        }

        displayLastUpdated = millis();

        String strokeString = UserConfig::language.Stroke;
        auto stringWidth = ossm->display.getUTF8Width(strokeString.c_str());

        displayMutex.lock();
        ossm->display.clearBuffer();
        ossm->display.setFont(Config::Font::base);

        drawShape::settingBar(UserConfig::language.Speed, next.speedKnob);

        if (isStrokeEngine) {
            switch (ossm->playControl) {
                case PlayControls::STROKE:
                    drawShape::settingBarSmall(ossm->setting.sensation, 125);
                    drawShape::settingBarSmall(ossm->setting.depth, 120);
                    drawShape::settingBar(strokeString, ossm->setting.stroke,
                                          118, 0, RIGHT_ALIGNED);
                    break;
                case PlayControls::SENSATION:
                    drawShape::settingBar("Sensation", ossm->setting.sensation,
                                          128, 0, RIGHT_ALIGNED, 10);
                    drawShape::settingBarSmall(ossm->setting.depth, 113);
                    drawShape::settingBarSmall(ossm->setting.stroke, 108);

                    break;
                case PlayControls::DEPTH:
                    drawShape::settingBarSmall(ossm->setting.sensation, 125);
                    drawShape::settingBar("Depth", ossm->setting.depth, 123, 0,
                                          RIGHT_ALIGNED, 5);
                    drawShape::settingBarSmall(ossm->setting.stroke, 108);

                    break;
            }
        } else {
            drawShape::settingBar(strokeString, ossm->encoder.readEncoder(),
                                  118, 0, RIGHT_ALIGNED);
        }

        /**
         * /////////////////////////////////////////////
         * /////////// Play Controls Left  ////////////
         * /////////////////////////////////////////////
         *
         * These controls are associated with stroke and distance
         */
        ossm->display.setFont(Config::Font::small);
        strokeString = "# " + String(ossm->sessionStrokeCount);
        ossm->display.drawUTF8(14, lh4, strokeString.c_str());

        /**
         * /////////////////////////////////////////////
         * /////////// Play Controls Right  ////////////
         * /////////////////////////////////////////////
         *
         * These controls are associated with stroke and distance
         */

        if (!isStrokeEngine) {
            strokeString = formatDistance(ossm->sessionDistanceMeters);
            stringWidth = ossm->display.getUTF8Width(strokeString.c_str());
            ossm->display.drawUTF8(104 - stringWidth, lh3,
                                   strokeString.c_str());
        }

        strokeString =
            formatTime(displayLastUpdated - ossm->sessionStartTime).c_str();
        stringWidth = ossm->display.getUTF8Width(strokeString.c_str());
        ossm->display.drawUTF8(104 - stringWidth, lh4, strokeString.c_str());

        ossm->display.sendBuffer();
        displayMutex.unlock();

        vTaskDelay(200);
    }

    vTaskDelete(nullptr);
};

void OSSM::drawPlayControls() {
    int stackSize = 3 * configMINIMAL_STACK_SIZE;
    xTaskCreate(drawPlayControlsTask, "drawPlayControlsTask", stackSize, this,
                1, &drawPlayControlsTaskH);
}

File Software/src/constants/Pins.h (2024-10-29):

#ifndef OSSM_SOFTWARE_PINS_CPP
#define OSSM_SOFTWARE_PINS_CPP

/**
 * Pin definitions for the OSSM
 *
 * These are all the hardware pins used by the OSSM.
 * These include pin definitions for Drivers, Buttons and Remotes
 *
 * To reference a pin, import this file and use the Pins namespace as follows:
 *
 * ```cpp
 * #include "constants/pins.cpp"
 *
 * Pins::button_in
 * Pins::Driver::motorStepPin
 * Pins::Homing::stopPin
 *
 * ```
 */

//TODO: separate pin definitions for OSSM Reference board and OSSM ICB

namespace Pins {

    namespace Display {
        // This pin is used by u8g2 to reset the display.
        // Use -1 if this is shared with the board reset pin.
        constexpr int oledReset = -1;

        // Pin used by RGB LED
        constexpr int ledPin = 48;
    }

    namespace Driver {
        constexpr int currentSensorPin = 4;

        // Pin that pulses on servo/stepper steps - likely labelled PUL on
        // drivers.
        constexpr int motorStepPin = 12;
        // Pin connected to driver/servo step direction - likely labelled DIR on
        // drivers. N.b. to iHSV57 users - DIP switch #5 can be flipped to
        // invert motor direction entirely
        constexpr int motorDirectionPin = 11;
        // Pin for motor enable - likely labelled ENA on drivers.
        constexpr int motorEnablePin = 13;

        // define the IO pin the emergency stop switch is connected to
        constexpr int stopPin = 14;
        // define the IO pin where the limit(homingStart) switch(es) are
        // connected to (switches in series in normally open setup) Switches
        // wired from IO pin to ground.
        constexpr int limitSwitchPin = -1;
    }

    namespace Wifi {
        // Pin for Wi-Fi reset button (optional)
        constexpr int resetPin = -1;
        // Pin for the toggle for Wi-Fi control (Can be targeted alone if no
        // hardware toggle is required)
        constexpr int controlTogglePin = 45;
    }

    /** These are configured for the OSSM Remote - which has a screen, a
     * potentiometer and an encoder which clicks*/
    namespace Remote {

        constexpr int speedPotPin = 7;

        // This switch occurs when you press the right button in.
        // With the current state of the code this will send out a "ButtonPress"
        // event automatically.
        constexpr int encoderSwitch = 17;

        // The rotary encoder requires at least two pins to function.
        constexpr int encoderA = 15;
        constexpr int encoderB = 16;
        constexpr int encoderPower =
            -1; /* Put -1 of Rotary encoder Vcc is connected directly to 3,3V;
                   else you can use declared output pin for powering rotary
                   encoder */

        constexpr int displayData = 5;
        constexpr int displayClock = 6;
        constexpr int encoderStepsPerNotch = 4;
    }
}
//first version of manufactured remote board has a error in schematic, displayData swapped with speedPotPin
#endif  // OSSM_SOFTWARE_PINS_CPP

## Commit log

2024-11-02 Removing hardware files and adding ICB sources
    [24mm_threaded_fleshlight_original_attachment v6.f3d, 24mm_threaded_fleshlight_original_attachment v6.stl, 25(.4)mm_tube_rosette_mount_v2.stl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]
2024-11-04 Prettify partition.csv
    [partition.csv]
